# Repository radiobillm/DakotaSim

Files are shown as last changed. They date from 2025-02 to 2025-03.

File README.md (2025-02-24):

# DakotaSim – Piper Dakota Flight Simulator

DakotaSim is a PA-28-235 flight simulator to match our real plane's G3X-based panel. 

[Project Wiki](docs/home.md) is extensive and includes:

- A hardware build with custom-fabricated hardware
- SketchUp models
- Arduino-based HID throttle, switch, and trim controls
- Custom Air Manager instruments
- Parts and prices detail

## Downloads
- [DakotaSim SketchUp](https://github.com/radiobillm/DakotaSim/releases/download/v2.0-sketchup/dakota-sim.skp)
- [Arduino Sketches and boards.txt](https://github.com/radiobillm/DakotaSim/releases/download/v1.0-arduino/DakotaSim-Arduino.zip)
- [AirManager for Dakota](https://github.com/radiobillm/DakotaSim/archive/refs/tags/v1.0-airmanager-garmin.zip)
- [AirManager for Garmin 255/345](https://github.com/radiobillm/DakotaSim/archive/refs/tags/v1.0-airmanager-garmin.zip)

## Resources
- [Parts and Pricing](https://github.com/radiobillm/DakotaSim/blob/main/parts.md)
- [Community Discussions](https://github.com/radiobillm/DakotaSim/discussions)
- [Submit an Issue](https://github.com/radiobillm/DakotaSim/issues)

## Older Versions

### Dakota Sim for Honeycomb 
- [Description](Dakota-Honeycomb.md)
- [Sketchup](https://github.com/radiobillm/DakotaSim/releases/download/v1.0-dakota-honeycomb/dakota-honeycomb.skp)
  
### Desktop Sim
- [Desktop Sim](Desktop-sim.md)

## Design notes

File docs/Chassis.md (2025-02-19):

# Volair Chassis 

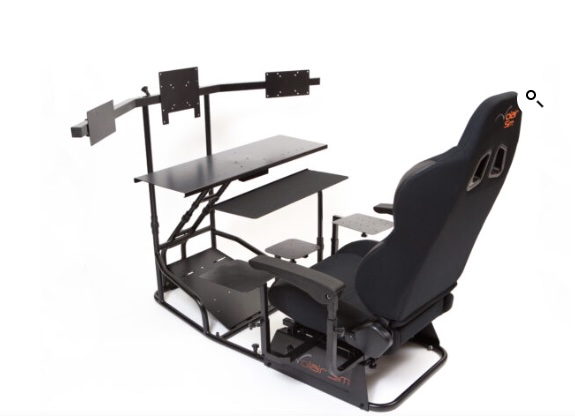
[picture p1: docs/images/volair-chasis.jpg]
Chasis


Volair’s Sim Chassis is sturdy and adjustable, the seat is comfortable.   The optional keyboard tray and armrests are nice.  I’ve not used any of the multiple plate mount attachments included.  

Their monitor support would be good for even a heavy single center monitor, but not for three.  I’ve replaced the monitor poles with rear table supports and built a floating shelf for the iTX computer case.

## Computer Shelf
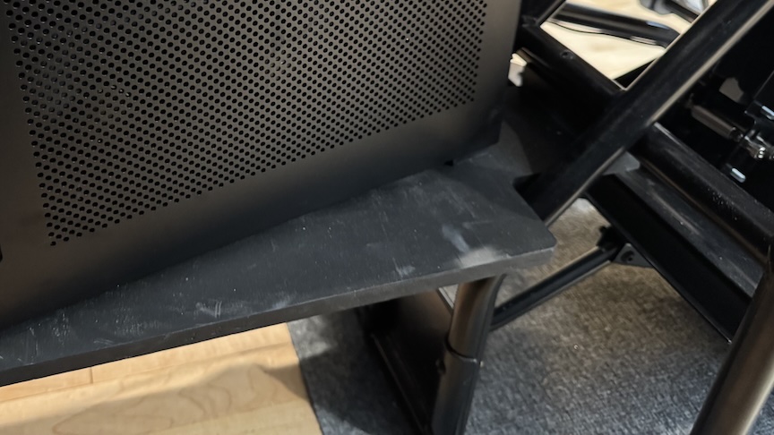
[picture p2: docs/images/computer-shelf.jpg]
Computer Self


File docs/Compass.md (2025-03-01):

# Compass

The whiskey-style Compass was purchased from SimWales (via caspajack on eBay), and it looks fantastic.

Mobiflight controls the compass, I had to adjust the suggested settings to use a Display Scale of 9000 and Transform $ * (-12.5).  The compass is powered with a USB 5V USB cable.

The compass stepper controller and ardunio are contained within a printed box that also holds the dimmer module.

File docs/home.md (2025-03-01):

# Dakota Flight Simulator

February 2025

Welcome to the documentation for my flight simulator project. This Wiki contains details about the construction, components, and software used in the simulator.

The sim was built to practice IFR flying using new avionics that match our real plane. It has also been a great opportunity to learn Arduino and explore my Onefinity CNC/Laser.

ChatGPT tells me that Piper has sold about 30,000 PA-28 series aircraft, compared to 45,000 Cessna 172/182 models. It’s surprising—and somewhat frustrating—for Piper pilots that most commercial flight sim products are Cessna-based. This project was built to create a sim that closely matches our plane.

The sim community is a gem.  After learning from so many projects and discussions, I felt guilty for never sharing my work.  This document includes the key components, build details, and lessons learned that I believe will be most helpful to others.

The current build would cost about $10,000. The project includes a breakdown of parts and prices.

## Front
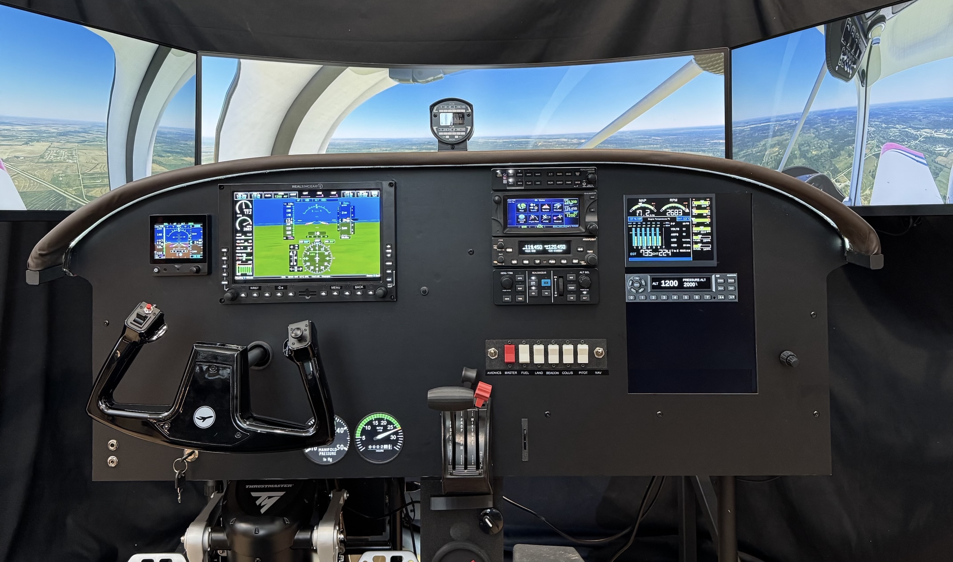
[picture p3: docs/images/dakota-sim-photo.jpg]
Dakota Sim


## Back
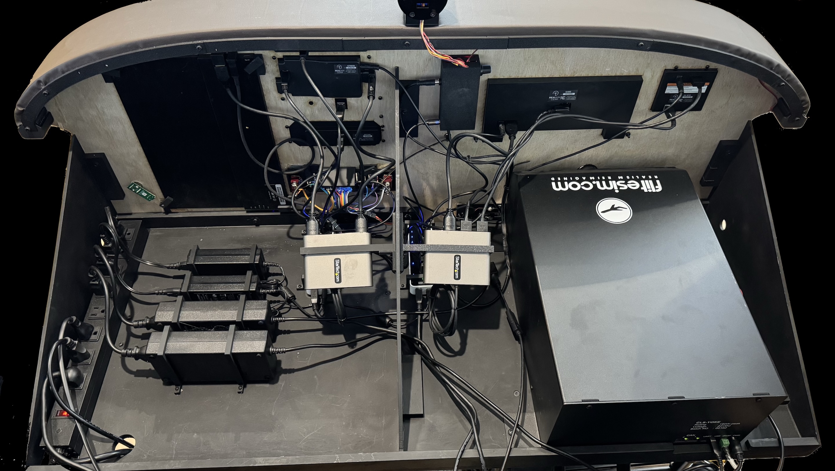
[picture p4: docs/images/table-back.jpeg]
Back of Panel


## Cockpit Structure
- [Avionics Panel](Panel.md) with laser cutting, auto wrap
- [Avionics Table](Table.md) with support, power, dimmer, hubs
- [Volair Chassis](Chassis.md) has a computer shelf
  
## Fabricated Controls
- [Throttle, Switch, & Panel Controls](Panel-Controls.md)
- [Center Stack , Brake, & Fuel](Center-Controls.md)
- [Trim & Flaps](Trim-flaps.md)
- [Compass](Compass.md)

## Arduinio
- [Arduino Hardware](Arduino.md)
- [Ardunio Software / FS2020](Arduino-sw.md)
  
## Other Purchased Hardware
- [RSG & Tigerfly Instruments](Instruments.md)
- [Flitesim Yoke & Thrustmaster Pedals](Yoke-pedals.md)
- [Monitors & Sound](Monitors-Sound.md)
- [Computer](Computer.md)

## Software
- [Software & Config Notes](Software.md)
- [Air Manger Instruments](AirManager.md)
- [SketchUp & Fabrication Files](SketchUp-Fabrication-Files)

## Parts List
- [Parts List & Pricing](Parts-Price.md)

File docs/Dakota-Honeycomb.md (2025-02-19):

# Dakota Sim with Honeycomb

In late summer of 2023 we bought a share of a PA-28-235 so I had a specific plane to target.  This second generation sim was a big upgrade to build a dedicated sim and recover my office desk.  It includes avionics to match our glass upgrade in the real-life plane. 

The heart of our new panel is a Garmin G3X and no X-Plane version is available so I moved to Microsoft and Windows. 

Details that are distinct from this older version may help those using standard Honeycomb throttle/yoke panels.

Dakota Sim with Honeycomb
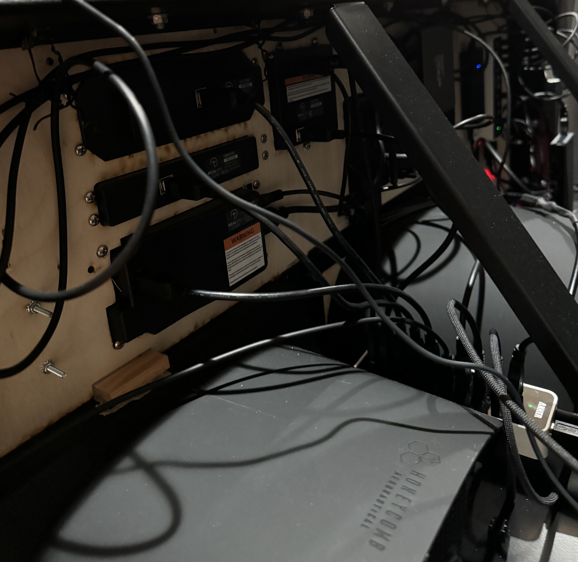
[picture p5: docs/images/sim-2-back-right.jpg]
Dakota Honeycomb Back

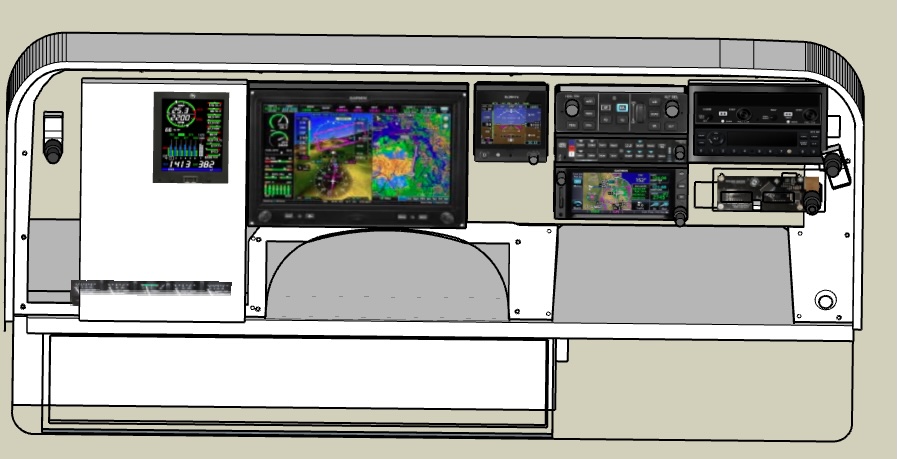
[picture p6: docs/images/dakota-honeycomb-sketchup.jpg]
Sketchup


## Panel
$500 [Volair panel](https://volairsim.com/product/volair-sim-avionics-panel-g1000/)

The Volair G1000 panel has a heavy-duty metal structure, back and table.  To fit my instruments I cut away most of the panel.  Into the frame I added a plywood back, cardboard center, and ACM front panel layers.

The -Honecomb Sketchup model has measurements from their panel made from test fitting cardboard itterations.

## Fabrication
$200 for [MakeATX](https://www.makeatx.com/custom-cutting) local laser cutting, 3 cardboard test iterations, final ¼” plywood back

$150 ACM front panel from [SendCutSend](https://sendcutsend.com/materials/acm/), great service 

## Panel and chassis
$600 Triple monitor stand from [Simfab](https://simfab.com/product/triple-monitor-mount-stand/), excellent quality

$1000 [Volair chassis](https://volairsim.com/product/volair-sim-flight-racing-sim-cockpit/) with arm rests and keyboard mount, excellent build

## Instruments
$1200 [G500](https://realsimgear.com/products/realsimgear-g500-avionics-panel	) from RealSimGear (originally for X-Plane with no G3X)

$550 [GTN650](https://realsimgear.com/products/realsimgear-gtn650-bezel-for-x-plane-p3d-and-fsx-steam) from RealSimGear

$350 [GFC500](https://realsimgear.com/products/realsimgear-gfc500-autopilot-for-x-plane-p3d-fsx) from RealSimGear

$350 [G5](https://realsimgear.com/products/realsimgear-g5-pfd-hsi-for-x-plane) from RealSimGear

$300 [GMA350](https://realsimgear.com/products/realsimgear-gma350-audio-panel-for-x-plane-p3d-fsx) from RealSimGear

$80 [Propwash Radio](https://www.propwashsim.com/)

## Panel LCD Displays
$70 [1920x1200](https://www.amazon.com/gp/product/B0DKFHZ8C8/) 14” left-side display for Air Manager compass, JPI engine, oil

$70 [1024x600](https://www.amazon.com/gp/product/B07VNX4ZWY/?th=1) 7” right-side touch display for Air Manager radio and transponder

$300 [1920x360](https://www.amazon.com/gp/product/B0CFY564ZQ) 24” low display for Air Manager fuel, manifold and tach

## Monitors and sound
$700 [Samsung Odyssey G9](https://www.amazon.com/gp/product/B0CP6HW894/) 49” Ultrawide monitor

$250 Two [Samsung 27” T35F](https://www.amazon.com/gp/product/B08FF3JQ28/) side monitors

$300 [Sonos Beam](https://www.sonos.com/en-us/shop/beam-b-stock-shadow), used Gen 1 (for an all Sonos-dude)

$85 [USB2GA Aviation Headset to USB Adapter](https://www.amazon.com/gp/product/B0CW3GLDM1/)

## Computer
In addition to the i9 running MSFS, I added this machine to Air Manager monitors

$230 MeLE [Mini PC](https://www.amazon.com/gp/product/B0CP3YL6J7/) for dedicated Air Manager

## Hubs, Power and Cables
$180 for two [StarTech USB to 4x HDMI](https://www.amazon.com/gp/product/B09BJWGPXR/)

$80 for two [Anker 10 Port 60W USB Hubs](https://www.amazon.com/gp/product/B00VDVCQ84/)

$21 [USB A to TOSLINK](https://www.amazon.com/gp/product/B0B2DBGKL3/r) for Sonos Beam audio

$20 [10A 12V Power supply](https://www.amazon.com/gp/product/B07MXXXBV8/) with custom hydra for RSG panel monitors

$57 [8 Outlet Metal Power Strip](https://www.amazon.com/gp/product/B0CJ55M1TH/)

$8 [12” USB-A Micro cable](https://www.amazon.com/gp/product/B095JZSHXQ/r)

$8 [12” USB-A to C cables](https://www.amazon.com/gp/product/B0BDFHBXQC/r)

$7 [18” HDMI cable](https://www.amazon.com/gp/product/B07ZC5Y3K2/r)

$9 [12” HDMI cables](https://www.amazon.com/gp/product/B0B5KN6853/)

$14 [6’ HDMI thin cables](https://www.amazon.com/gp/product/B00T58JLPI/r)
$10 [Displayport to HDMI adapters](https://www.amazon.com/gp/product/B09MTKHFKR/)

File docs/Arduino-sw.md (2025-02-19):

# Ardunio Software

One goal was to reduce software stacks which is why the input-only controls are HID and configured in MSFS.  ChatGPT wrote those the software software, it’s a marvelous tool for handling details and learning.

With FS2024 I may use MobiFlight or spad.next to better map and maintain.

Three Arduinos cover all input-only controls using the Joystick library.  The project includes code for each:
* Arduino Pro Throttle, Switch, TOGA, Carb Heat
* Arduino Micro Pro Trim and Flaps
* Arduino Micro Pro Parking Brake, Key/Start, Fuel Selector, and Rudder Trim

[Arduino Sketches and boards.txt](https://github.com/radiobillm/DakotaSim/releases/download/v1.0-arduino/DakotaSim-Arduino.zip)

## HID to Microsoft FS Controls

### Switch-Throttle
| Control | Button | FS-Control |
|---|---|---|
| Throttle | x | Throttle Axis |
| Mixture | y | Mixture Axis |
| Propeller Axis | z | Propeller Axis |
| Avionics Master 1 On | 2 | Avionics Master 1 On |
| Avionics Master 1 Off| 1 | Avionics Master 1 Off  |
| Master Battery On | 4 | Master Battery On |
| Master Battery Off | 3 | Master Battery Off |
| Set Electric Fuel Pump| 6 | Set Electric Fuel Pump |
| Set Electric Fuel Pump Off | 5 | Set Electric Fuel Pump Off |
| Landing Lights On | 8 | Landing Lights On |
| Landing Lights Off | 7 | Landing Lights Off |
| Beacon Lights On | 10 | Beacon Lights On |
| Beacon Lights Off | 9 | Beacon Lights Off |
| Strobes On | 12 | Strobes On |
| Strobes Off | 11 | Strobes Off |
| Pitot Heat On | 14 | Pitot Heat On |
| Pitot Heat Off | 13 | Pitot Heat Off |
| Nav Lights On | 16 | Nav Lights On |
| Nav Lights Off | 15 | Nav Lights Off |
| Set Anti Ice On | 18 | Set Anti Ice On |
| Set Anti Ice Off | 17 | Set Anti Ice Off |
| Auto Throttle to GA  | 19 | Auto Throttle to GA |

### Brake-Fuel
| Control | Key | FS-Control |
|---|-----|---|
| Magnetos Off | 1 | Magnetos Off |
| Magnetos Left | 2 | Magnetos Left |
| Magnetos Right | 3 | Magnetos Right |
| Magnetos Both | 4 | Magnetos Both |
| Magnetos Start | 5 | Magnetos Start |
| Parking Brakes On | 6 | Parking Brakes On |
| Parking Brakes Off | 7 | Parking Brakes Off |
| Fuel Selector 1 Off | 8 | Fuel Selector 1 Off |
| Fuel Selector 1 Left Aux | 9 | Fuel Selector 1 Left Aux  |
| Fuel Selector 1 Left  | 10  | Fuel Selector 1 Left |
| Fuel Selector 1 Right | 11  | Fuel Selector 1 Right |
| Fuel Selector 1 Right Aux| 12  | Fuel Selector 1 Right Aux |
| Rudder Axis | z | Rudder Axis |

### Trim-Flaps
| Control | Trim/Flaps | FS-Control |
|---|---|---|
| Set Elevator Trim Axis | x | Set Elevator Trim Axis |
| Retract Flaps | 04 | Retract Flaps |
| Flaps 1 | 103 | Flaps 1 |
| Flaps 2 | 302 | Flaps 2 |
| Flaps 3 | 451 | Flaps 3 |

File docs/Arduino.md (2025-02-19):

# Ardunio Hardware

Before this project, I had no prior experience with Arduino or circuit board assembly.  

Initially, I soldered IDC ribbon cables directly to the Arduino pins, using a separate connector for each control. Later, for the two additional Arduino Pros, I switched to using connectors soldered on the Arduino.

Renaming the USB HID device requires updating the boards.txt file, one is included.

See the software info

## Pin Mapping and Wire Bundles

This table documents the pin assignments and controls for the switch-throttle micro setup.

### Switch-Throttle - Micro

| PIN | USB | WIRE-COLOR | Cable |
|-----|-----|---|---|
| D13  | | Pitot Off | green |
| 3V | AREF| | |
| A0 | | Throttle | green |
| A1 | | Mixture | yellow |
| A2 | | Prop | orange |
| A3 | | Carb Heat On | blue |
| A4 | | Carb Heat Off  | purple |
| A5 | NC  | | |
| 5V | | 5V | red |
| GND  | | GND | brown |
| VIN  | | | |
| D14  | | GA | brown |
| D15  | | Nav Off | orange |
| D12  | | Avionics On | white |
| D11  | | Avionics Off | grey |
| D10  | | Master On | purple |
| D9 | | Master Off | blue |
| D8 | | Fuel On | green |
| D7 | | Fuel Off | yellow |
| D6 | | Landing On | orange |
| D5 | | Beacon On | brown |
| D4 | | Beacon Off | white |
| D3 | | Collision On | grey |
| D2 | | Landing On | red |
| GND  | | GND | black |
| RESET| | | |
| D0 | | Collision Off  | purple |
| D1 | | Pitot On | blue |
| D17  | | | |
| D16  | | Nav On | yellow |

### Brake-Fuel Pro Micro

| PIN | USB | WIRE-COLOR | Cable |
|---|-----|---|---|
| TX/RX/GND| | black | Key+Brake|
| GND | | grey | Key |
| D2 | | purple | Key |
| D3 | | blue | Key |
| A6/D4 | | green | Key |
| D5 | | yellow | Key |
| A7/D6 | | orange | Key |
| D7 | | | |
| A8/D8 | | orange | Rudder |
| A9/D9 | | | 7-12V |
| GND | | black | Rudder |
| RST | 5V  | orange | Rudder |
| A3/D21  | | brown | Fuel |
| A2/D20  | | red | Fuel |
| A1/D19  | | orange | Fuel |
| A0/D18  | | yellow | Fuel |
| D15 | | green | Fuel |
| D14 | | yellow | Park |
| D16 | | red | Park |
| A10/D10 | | | |

### Trim-Flaps Pro Micro

| PIN | USB | WIRE-COLOR | Cable |
|---|-----|---|---|
| TX/RX/GND| GND | black | Flaps | 
| D2 | | white | Flaps |
| D3 | | grey | Flaps |
| A6/D4 | | purple | Flaps |
| D5 | | blue | |
| A7/D6 | | | |
| D7 | | | |
| A8/D8 | | black | Trim |
| A9/D9 | | | 7-12V |
| GND | RST | | |
| 5V | | | |
| A3/D21  | | | |
| A2/D20  | | | |
| A1/D19  | | | |
| A0/D18  | | | |
| D15 | | | |
| D14 | | | |
| D16 | | | |
| A10/D10 | | | |

### Compass Pro Micro

| PIN | USB | WIRE-COLOR | Cable |
|---|-----|---|---|
| TX/RX/GND| | | |
| GND | | | Compass  |
| D2 | | | |
| D3 | | | |
| A6/D4 | | | |
| D5 | | | |
| A7/D6 | | | |
| D7 | | | |
| A8/D8 | | | |
| A9/D9 | | | 7-12V |
| GND | RST | 5V | |
| 5V | | | |
| A3/D21  | | | Compass  |
| A2/D20  | | | Compass  |
| A1/D19  | | | Compass  |
| A0/D18  | | | Compass  |
| D15 | | | |
| D14 | | | |
| D16 | | | |
| A10/D10 | | | |

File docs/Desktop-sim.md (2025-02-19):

# Desktop Sim

Desktop Sim

I retired in early 2023 and decided to resume flying after a 30 year break.  The first step was setting up a desktop sim. 

My first iteration was X-Plane based system on my office desk which had a Mac Studio and Samsung ultrawide monitor.  The only item still used from that version is my Air Manager license.

Below are the components:

$60 [X-Plane](https://www.x-plane.com/) 

$30 AeroSphere [PA-28-235](https://store.x-plane.org/Piper-PA-28-235-Charger-Cherokee-235_p_1605.html) to match my real life plane

$750 Honeycomb [yoke](https://flyhoneycomb.com/collections/bestseller/products/alpha-flight-controls) and [throttle](https://flyhoneycomb.com/collections/bestseller/products/bravo-throttle-quadrant) plus Logitech [rudder pedals](https://www.logitechg.com/en-us/products/flight/flight-simulator-rudder-pedals.945-000024.html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)

$30 Rudder pressure rolls back the Aeron chair, added [locking chair casters](https://www.amazon.com/gp/product/B0BKLSQVJ4/)

$300 [Air Manager](https://www.siminnovations.com/air-manager/) and [Knobsters](https://www.siminnovations.com/shop/knobster/) made realistic instrument use

$120 Moved instruments to a [14” portable touch display](https://www.amazon.com/gp/product/B0C4TCHK1S/r)

$100 More panel display from an old iPad and [Luna display dongle](https://shop.astropad.com/collections/luna-display-mac-and-pc?) 

$300 Added Mac-compatible [GNS530 from FlightSimBuilder](https://flightsimbuilder.com/products/gns-530-fs2020-campatabl) to learn buttonology

$70 Stay Level [touch bracket](https://staylevelavionix.com/shop/touch-bracket), soon replaced with…

$20 Fabricated [channel](https://www.dkhardware.com/satin-anodized-1-2-aluminum-u-channel-dv750a-ccp24-24-stock-length-product-3696857.html) for glass table to mount yoke and throttle under glass desk for space

$45 Added 3 [flexible phone mounts](https://www.amazon.com/gp/product/B07726TH68/) to hold displays and the 430, these worked well

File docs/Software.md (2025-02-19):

# Dakota Sim Software

## RV-10
The RV-10 was early with G3X and TDS GTN support.  Its power and handling are similar to the low-wing Piper Dakota we fly.

## TDS GTNxi Pro

The GTN650 was an essential piece in my setup. My move from X-Plane to MSFS was largely driven by the need for a Garmin G3X that integrated properly with the GTN.  The current G3X from Asobo is very good and I’m grateful to TDS for integrating with it.

TDS builds a high quality instrument and their support has been superb, both for me and others on Discord.  They don’t over-promise and they take actual bugs seriously.

One downside is that each time you load MSFS you need to use TDS admin to set the nav source from the 750 to 650.  Another downside is that I’m still not able to maximize the window in the RSG screen without a title bar.  Either the bar shows and the window can be sized, or the bar is hidden and the app window is about 30% of the size needed. I simply pull the title bar outside the instrument.

I’ve used the PMS version which works not as well but mostly was not integrated with the G3X.  My first GTN was for X-Plane from RealityXP, it worked OK but their constant license renewal was annoying.

## MSFS Popup Panel Manager

Thanks to Stanley Kwok for creating and sharing his popout manager. This free tool makes it possible to use a touch display and also automates popout and placement when flying.  

It’s hard to understand how Microsoft continues to ignore touch instruments.

Unfortunately, I still need a mouse on standby because my G500 panel frequently ignores touch input on the left side of the display. This isn’t a hardware issue—other applications recognize touch input in the same area. Since the G3X is my primary instrument, this matters quite a bit and is one of the main reasons I moved from X-Plane to MSFS.

## MobiFlight

MobiFlight is an open source bridge between hardware and sims.  It’s essential for my GNC255 radio built by a MobiFlight expert. MobiFlight also controls the compass.  I don’t know the software yet but for better control options I am considering moving my own arduino instruments to it.

## RealSimGear MSFS Device Interface

Since my setup includes five RealSimGear instruments, I rely heavily on their MSFS device interface. I’m glad to see they’ve become more active on Discord and in support channels again, though their primary focus now appears to be commercial SR22 simulators.

My setup still includes a G500 panel that I originally purchased during my X-Plane era.

Through experimentation, I’ve remapped this hardware to function with G3X commands, using the command.ini file. To improve usability, I’ve labeled certain G500 buttons for G3X functions.

While this setup is a little janky, it works well enough that I don’t need to buy another $1,200 RealSimGear instrument or build a custom one from scratch.

The command.ini in the project also has GMA350 audio panel knobs, the default only maps critical buttons.

I suspect the RealSimGear device interface is responsible for the total loss of controls that occurs about 30 minutes into a flight session in MSFS.

Controls only return if I open the Controls menu and then exit back into the flight, which suggests an interface-related issue. Since this only happens when RSG is loaded, I’m considering switching to spad.next as an alternative.

## LittleNavMap

LittleNavMap is excellent for quickly creating flight plans, which I sometimes export to the GTN.

I also use it to monitor my flight progress and manage descent slopes efficiently.

## RealVNC

Spending hours in the cockpit chair with a keyboard tray and a sea of monitors can be tiring.  RealVNC has been great for some projects working upstairs in an office setting.  Real VNC also lets me find lost monitors and work when the screen is covered by panel.

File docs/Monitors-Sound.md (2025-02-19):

#Monitors and Sound

## Main Monitors

name

Since I was already happy with a previous model, I upgraded to Samsung’s 49” Ultrawide Odyssey G9 as my center monitor, paired with two Samsung 27” side monitors.  

## Monitor Stand
name

The SimFab Triple Mount monitor stand is beefy and good without angled front but without side stands. Vertically aligning side monitors took all the adjustment available and then some to match the ultrawide center screen.

All three monitors use HDMI on the monitor connected to one HDMI and two DP ports with adapters on the 4080 card.  For some reason, the ultrawide monitor’s DisplayPort connection was not recognized, and after spending too much time troubleshooting, I gave up and used HDMI instead.  Also, I goofed by buying an Intel i9 processor without graphics.  

## Panel Monitors

The panel includes six monitors, all powered through a USB-to-HDMI adapter:

* RealSimGear G500, GTN, and G5
* A low-mounted display for Manifold and Tach gauges powered by USB-C
* A right-side monitor for the JPI Engine Monitor and Transponder

This setup mostly works well, but occasionally Windows 10 forgets the display arrangement or loses touchscreen functionality.  

In an earlier setup, I had nine total displays, but Windows 10 frequently dropped them from the configuration. To fix this, I added a dedicated mini PC to handle Air Manager instruments. Now that I’ve reduced the number of displays, the mini PC is no longer necessary.

## Sound

A Sonos Beam works well using a USB-TOSLink-HDMI connection.  The beam rest on L brackets fabricated to hang from the monitor stand.

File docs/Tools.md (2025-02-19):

This major upgrade was the excuse needed to upgrade my shop with these tools:

$6800 [Onefinity Foreman](https://www.onefinitycnc.com/product-page/elite-series-foreman-48-x48-cut-area) 4’x4’ CNC, [PwCNC spindle](https://pwncnc.com/products/spindle), [44W laser](https://www.onefinitycnc.com/product-page/onefinity-j-tech-44w-octo-pro-laser-worlds-most-powerful-diode-laser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), and dust boot

$950 [FlexiSpot E7Q](https://www.flexispot.com/flexispot-odin-4-leg-standing-desk) 4-leg standing to park my CNC above my planner and joiner

$840 [Bambu P1P](https://us.store.bambulab.com/products/p1p) 3D printer, enclosure upgrade (order mistake, they would not exchange)

I replaced the panel, table, yoke, throttle, rudder pedals and radio.  I don’t need all the Air Manager monitors nor the Air Manager computer.  I’m using all the instruments and especially design and layout lessons from the prior panel.

You can see the total products and prices used and build details in the main section above.

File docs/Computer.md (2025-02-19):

# Computer

Built from the parts list below including an i9 and 4080, performance is good enough to use mostly max settings with three monitors plus five in the panel.  The system was originally purchased for under my office desk, otherwise the small case is not worth the careful work squeezing components together.

I mistakenly ordered an i9 without graphics.

## PC Components

| Component | Product | Price | Where |
|---|---|---|---|
| **CPU** | [Intel Core i9-14900KF 3.2 GHz 24-Core Processor](https://pcpartpicker.com/product/MJRFf7/intel-core-i9-14900kf-32-ghz-24-core-processor) | $416.94 | [Amazon](https://www.amazon.com) |
| **CPU Cooler** | [Deepcool LT520 85.85 CFM Liquid CPU Cooler](https://pcpartpicker.com/product/dqXJ7P/deepcool-lt520-8585-cfm-liquid-cpu-cooler) | No Prices Available | |
| **Thermal Compound** | [Arctic Silver 5 High-Density Polysynthetic Silver 3.5 g Thermal Paste](https://pcpartpicker.com/product/gJmFf7/arctic-silver-5-high-density-polysynthetic-silver-35-g-thermal-paste) | $7.95 | [Amazon](https://www.amazon.com) |
| **Motherboard** | [Asus ROG STRIX B760-I GAMING WIFI Mini ITX LGA1700 Motherboard](https://pcpartpicker.com/product/vVy2FT/asus-rog-strix-b760-i-gaming-wifi-mini-itx-lga1700-motherboard) | $189.99 | [Newegg](https://www.newegg.com) |
| **Memory** | [Corsair Vengeance 32 GB (2 x 16 GB) DDR5-6400 CL32 Memory](https://pcpartpicker.com/product/XqgFf7/corsair-vengeance-32-gb-2-x-16-gb-ddr5-6400-cl32-memory) | $102.99 | [Newegg](https://www.newegg.com) |
| **Storage** | [Crucial P5 Plus W/Heatsink 2 TB M.2-2280 PCIe 4.0 X4 NVME Solid State Drive](https://pcpartpicker.com/product/xFmmP6/crucial-p5-plus-wheatsink-2-tb-m2-2280-pcie-40-x4-nvme-solid-state-drive) | $169.00 | [Amazon](https://www.amazon.com) |
| **GPU** | [Asus ProArt GeForce RTX 4080 16 GB Video Card](https://pcpartpicker.com/product/ff66Mp/asus-proart-geforce-rtx-4080-16-gb-video-card) | No Prices Available | |
| **Case** | [Lian Li A4-H20 X4 Mini ITX Desktop Case](https://pcpartpicker.com/product/ff66Mp/lian-li-a4-h20-x4-mini-itx-desktop-case) | $154.99 | [Amazon](https://www.amazon.com) |
| **Power Supply** | [Corsair SF750 (2018) 750 W 80+ Platinum Certified Fully Modular SFX Power Supply](https://pcpartpicker.com/product/ff66Mp/corsair-sf750-2018-750-w-80-platinum-certified-fully-modular-sfx-power-supply) | No Prices Available | |

### Base Total: **$1044.86**

[Full PCPartPicker List](https://pcpartpicker.com/list/qsLdJy)

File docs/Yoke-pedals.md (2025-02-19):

# Flitesim Force Yoke

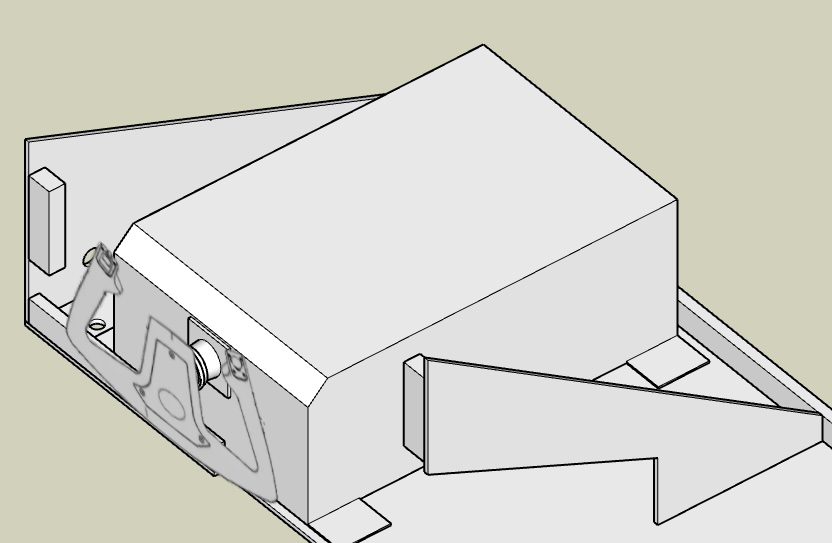
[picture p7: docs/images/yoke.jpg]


The Flightsim Force Yoke works well and brings a fun realistic dimension flying the sim.  The yoke box is much bigger than a Honeycomb which became the final straw forcing me to build a fully custom table, panel, and glare shield.

# Thrustmaster TPR Pedals

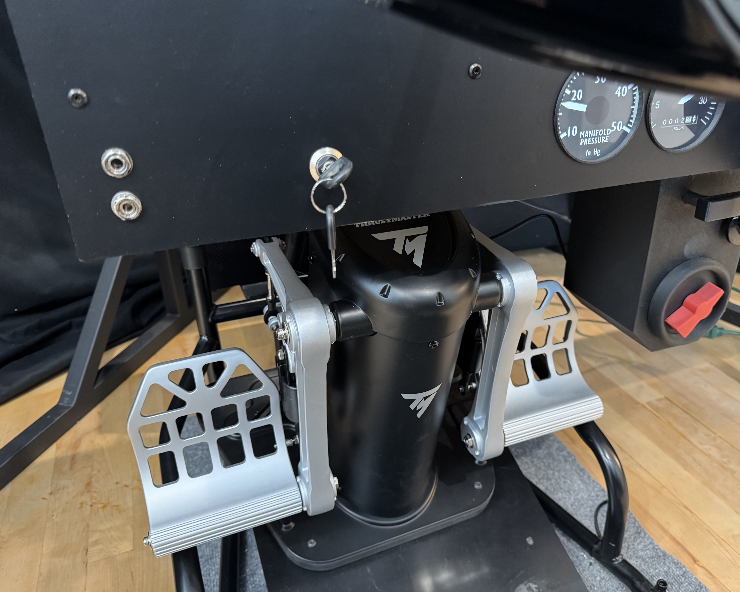
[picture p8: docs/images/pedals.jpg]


Thrustmaster TPR pedals have worked well so far as a nice upgrade from the Logitech set.  The Volair chassis has a framed well area and the pedals are designed for a flat floor.  I solved it by cutting a ¾” spacer that matched the Thrustmaster base.  The spacer has threaded inserts that align with the top Volair slots and an extra hole drilled below, then inserts for the four Thrusmaster base bolts.  This approach has worked well so far even while the right pedal almost hits my center box.

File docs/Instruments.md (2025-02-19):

# Insrtruments

## GNC255 Radio

One of my favorite devices in this build is the GNC255 radio, designed and built by Tigerfly.. I have an early build and don’t know if it will be a product.  You can usually find Tigerfly helping others on the MobiFlight Discord.

The radio has realistic knobs and buttons, a bright white OLED display and photo sensor for dimming.  Like the real Garmin, Tigerfly’s software includes frequency database lookup.  

Tigerfly was especially helpful getting me started with MobiFlight and I hope he’ll extend the line with a matching transponder and/or share the design.

## RealSimGear

The setup includes these instruments

* G5 works well with the air manager instrument with buttons mapped
* G500 is from an earlier sim and for my G3X, I don’t love it
* GTN650 works well except the home button is fake
* GFC500 AutoPilot is very good, except their vertical trim knob is flimsy
* GMA350 Audio works, I don’t see on their website anymore 

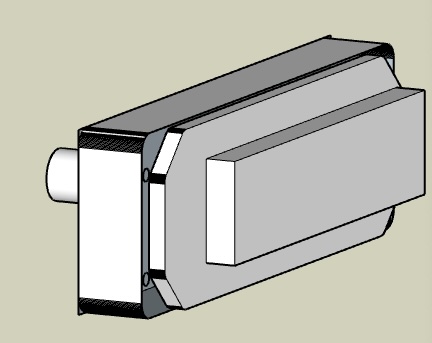
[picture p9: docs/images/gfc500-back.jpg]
GFC500 Model


Sketchup models are organized to use for 3d planning or just keeping the faceplate-cut to export for laser or cnc.

## Compass

The whiskey-style Compass was purchased from SimWales (via caspajack on eBay), and it looks fantastic.

Mobiflight controls the compass, I had to adjust the suggested settings to use a Display Scale of 9000 and Transform $ * (-12.5).  The compass is powered with a USB 5V USB cable.

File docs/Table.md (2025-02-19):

# Avionics Table

## Support Table
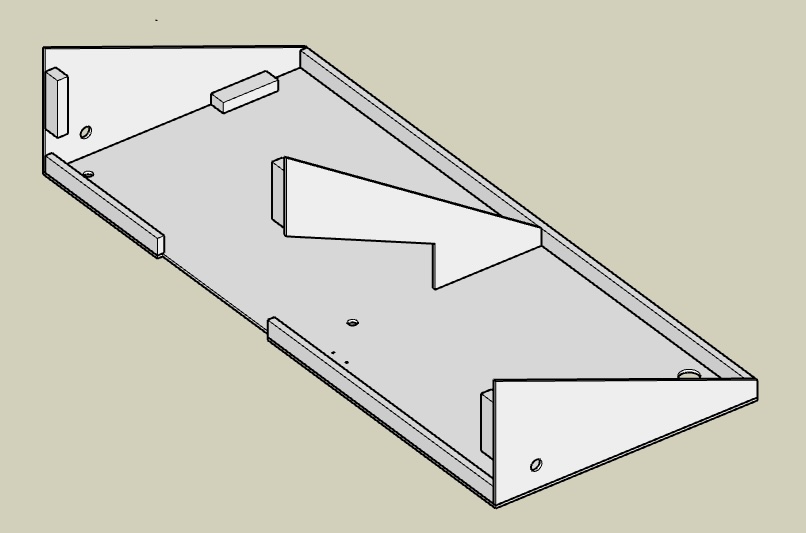
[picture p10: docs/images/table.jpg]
Avionics Table


The support Table is ½” plywood with edge and side pieces to replace the chassis metal. 

The side pieces are laser cut from 5.2mm plywood at 7mm/sec.  Laser lines etched into the table base made it clear where to cut and align the rail, sides and blocks.

The panel and table are setup for a left side yoke to be centered on the chair. The left side metal yoke box and the right side metal power strip help keep the assembly rigid. 

For support I replaced the original chassis monitor stand.  A 3/4”x24” threaded water pipe was cut in half and flanges attached to each end.  Those fit perfectly into the chassis to support the table.  The table and supports are painted flat black.  M6 bolts attach the table to the flange and front metal square tube, these holes are drilled after aligning and squaring the table but not in the.  A right-side leg supports the overhand and keeps the table stable.

## Power and Hubs

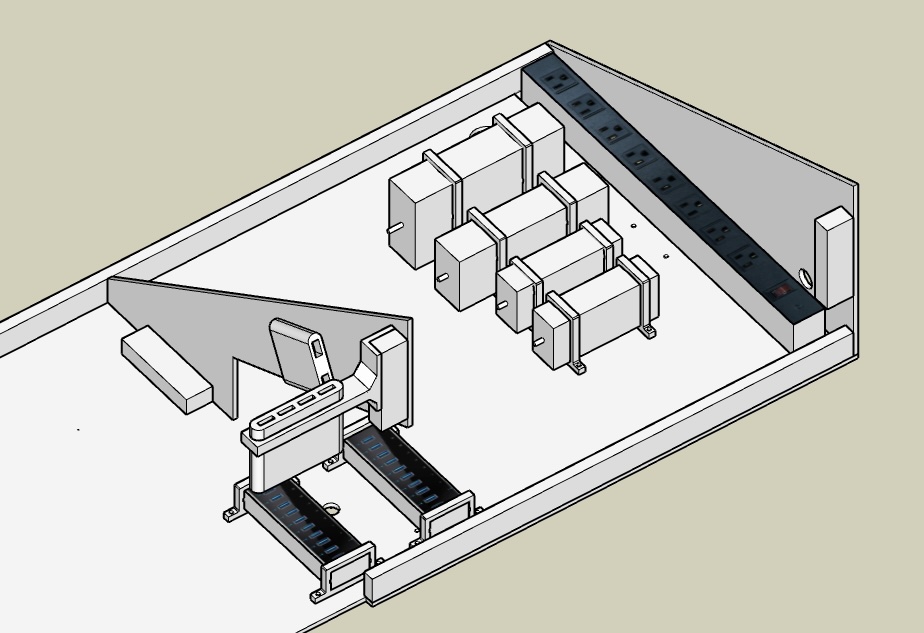
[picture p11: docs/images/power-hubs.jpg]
Power and Hubs


For aesthetics and easier troubleshooting I took time for the component layout above and under the table and designed and printed holders for power supplies, USB hubs, and HDMI adapters.

## LED Dimmer
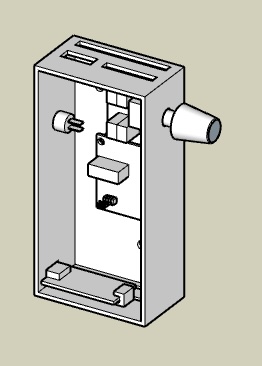
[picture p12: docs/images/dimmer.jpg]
LED Dimmer and Compass Arduino


A printed box with lid mounted on the back of the panel houses an Arduino Pro Micro and compass stepper motor driver plus a dimmer connected to the compass and under-glare shelf lighting.  A hydra end from the 12V power supply powers the dimmer.

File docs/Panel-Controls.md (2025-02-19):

# Fabricated Controls
## PA28 Throttle

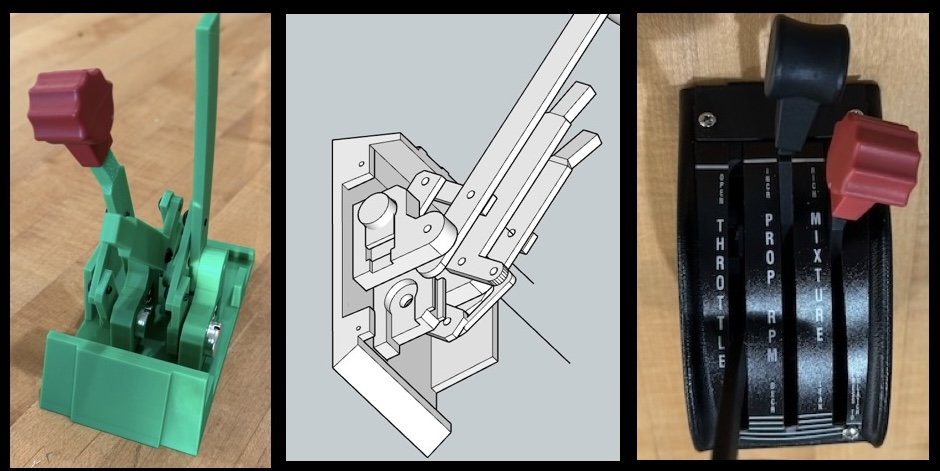
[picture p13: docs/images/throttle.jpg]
Custom PA-28 Throttle


I started by buying a real replacement throttle assembly trim and label, then designed and 3D printed the body.  

To fit the closely spaced throttle, prop, and mixture levers, I used bellcranks to offset the potentiometers.

The M4 screws into 3mm PLA holes were not strong enough on their own and required glue for reinforcement. Threaded inserts would be a better solution, as the tight space makes soldering and adjustments difficult.

Label strips are glued to the top of the trim cover under a printed trim plate.

## Switch Panel

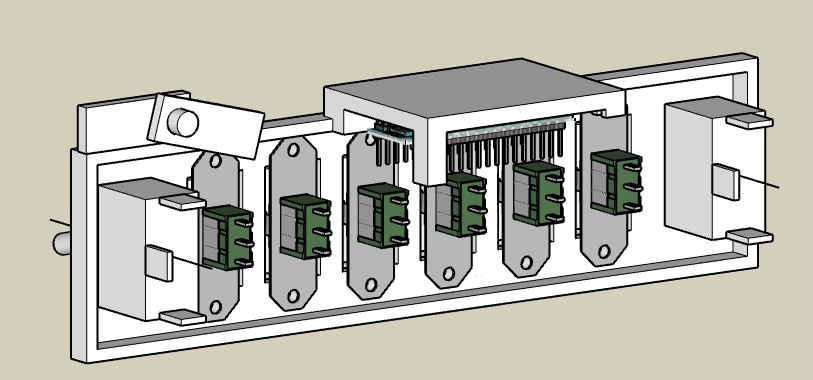
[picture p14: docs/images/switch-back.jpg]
Switch Panel Back


The hard part for the switch panel was sourcing rocker switches that match a real PA28.  I ordered a few alternatives but never found half-width rockers that could be ganged together to match the real set, nor found suitable grey covers.  

As a future improvement, I plan to laser engrave labels onto the switch covers for a more authentic look.

An Arduino Micro in the switch panel handles the switches, throttle, Carb Heat lever, and TOGO button. 

## Carb Heat

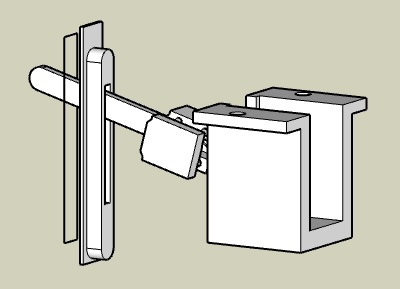
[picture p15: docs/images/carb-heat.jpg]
Carb Heat Lever


The Carb Heat lever is printed to sandwich the end of a metal toggle, the assembly also has a switch holder under the table.  A printed panel trim insert keeps the lever sliding vertically with a realistic feel.  MSFS offers Anti Ice On or Off, but no variable carb heat setting like a real PA28.

### Key Switch

I ordered the SimWales Key Switch from caspajack on eBay. The spring mechanism is well-designed, and the build quality is excellent.

One challenge was the table height meant moving the switch a little lower than in real life, even after cutting off the top of the assembly. The switch was disabled and the faceplate removed.  When reassembling I first aligned the key position and then the pin so it hits the spring on start. 

## Headset

The headset speaker and microphone jacks are connected via a USB Aviation adapter.

Installation Details:

* The adapter’s casing was removed, allowing me to use the jack nuts directly on the panel.
* Since the panel is ¼” thick, a relief pocket is needed on the backside (not currently included in the model).
* The USB board is glued to the back of the panel, as it lacks a dedicated case.

A prior ACM panel grounded the mic so it became unusable with PilotEdge, which was solved by printing bushings to insulate the jacks.  This bushing is unnecessary with plywood.

## Bezels

Simple bezels are printed for the yoke, manifold, and tach gauge, carb heat and togo switch openings.  I may build a bezel for the JPI Engine monitor.

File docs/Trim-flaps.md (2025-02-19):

# Trim and Flaps

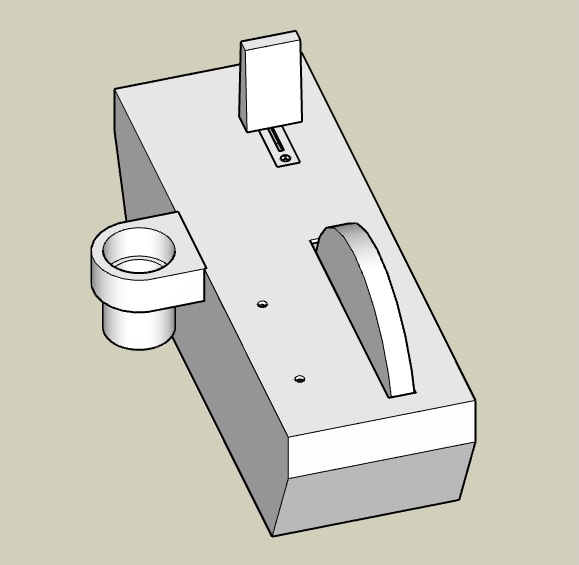
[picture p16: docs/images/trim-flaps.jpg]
Trim and Flaps


For a more realistic layout, I mounted an Elevator Trim box on the right side of the chair, where a pole mount normally holds the keyboard tray.  The box has a Trim Wheel, 4-position Flaps Paddle.  Inside the box an Arduino Micro is glued with the USB port facing down. 

The Trim Wheel, potentiometer, and switch were salvaged from a Desktop Aviator unit I purchased on eBay.

I may upgrade to a powered trim wheel with a geared position indicator in the future.  PA28 pilots will recognize that flaps are set with a long floor-mounted lever, the 172- flap lever is not realistic but at least it is centered near the floor.

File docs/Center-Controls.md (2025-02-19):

# Center Stack Controls

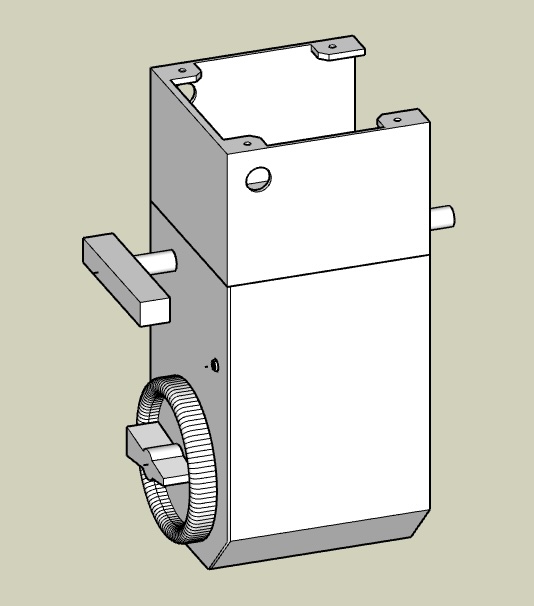
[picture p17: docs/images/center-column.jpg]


A bolted support box under the table houses:

✔ Parking Brake

✔ Fuel Selector Switch

✔ Rudder Trim

✔ Arduino Pro (which also controls the key switch)

Due to the limitations of my 255mm 3D printer bed, the column is built from two stacked boxes. The parking brake is mounted to the ceiling of the lower box.

However, the top box is too small to allow easy internal access. A better approach would be to side-mount the brake and leave an open column for easier maintenance.

The Arduino is floating with no mount, it also controls the key switch.

## Parking Brake 

I ordered the SimWales Parking Brake (designed for a Cessna 172) from caspajack on eBay, and it works well.

However, Parking Brake On and Off controls do not function correctly in either the Cessna 172 or RV-10. As a workaround, I mapped the Off control to Parking Brake Toggle for reliable operation.

The brake main rod stop was removed to remove the faceplate.  Be careful when rotating the brake assembly to preserve normally in and brake-off horizontal, vs pull and rotate brake-on vertical.  The switch pin can be flipped to an alternate hole.

## Fuel Selector 

The Fuel Selector switch is simply a trim piece over a 5-selector switch.  

On a real Piper PA-28-235, the fuel selector is located on the center firewall and has five fuel positions:

1. Off
2. Left Tip
3. Left Main
4. Right Main
5. Right Tip

I was unable to find any published designs for the plastic trim piece, nor could I find an MSFS Dakota or any PA-28 with a four-tank configuration.

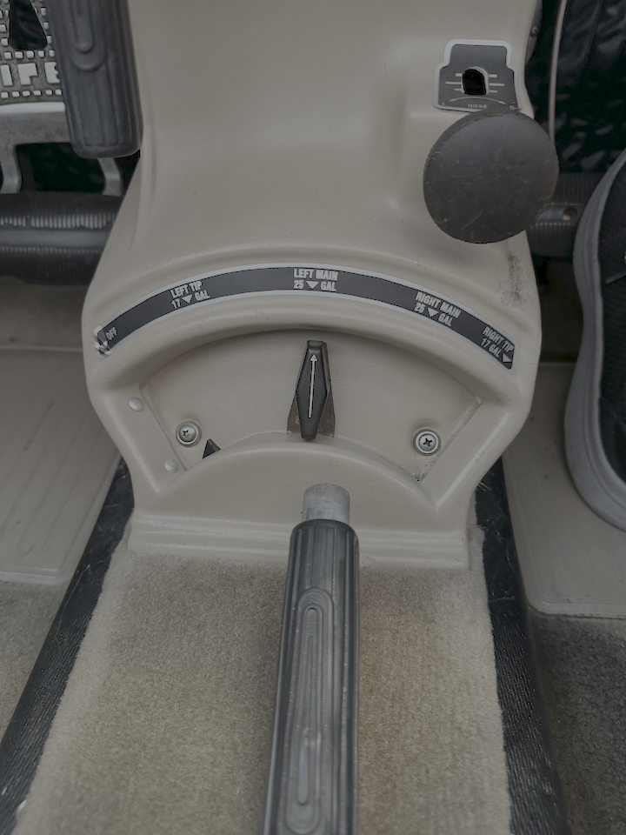
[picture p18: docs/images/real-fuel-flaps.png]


## Rudder Trim

The rudder trim uses a potentiometer identical to those used for the throttle levers. It is mounted with a custom-printed bracket for the center column.

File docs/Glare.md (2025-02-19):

# Glare Shield 

The glare shield has been the most time-consuming part of the build. My trepidation building one had me hacking the Volair panel for too long. But my first glare shield is only OK.

## Back Structure

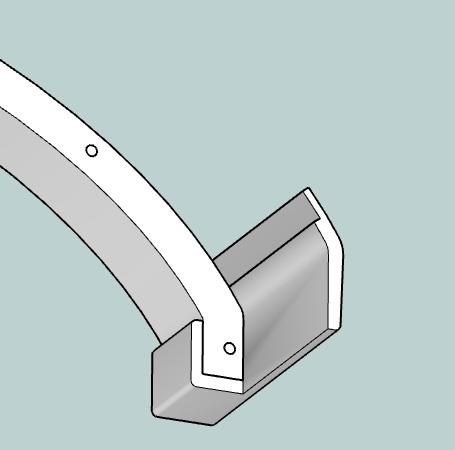
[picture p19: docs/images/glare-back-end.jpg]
Glare Sheld Back


The curved vertical back of the glare shield (glare-base layer) is built from two laminated ½” plywood pieces, cut on the CNC. 

## Horizontal Shelf

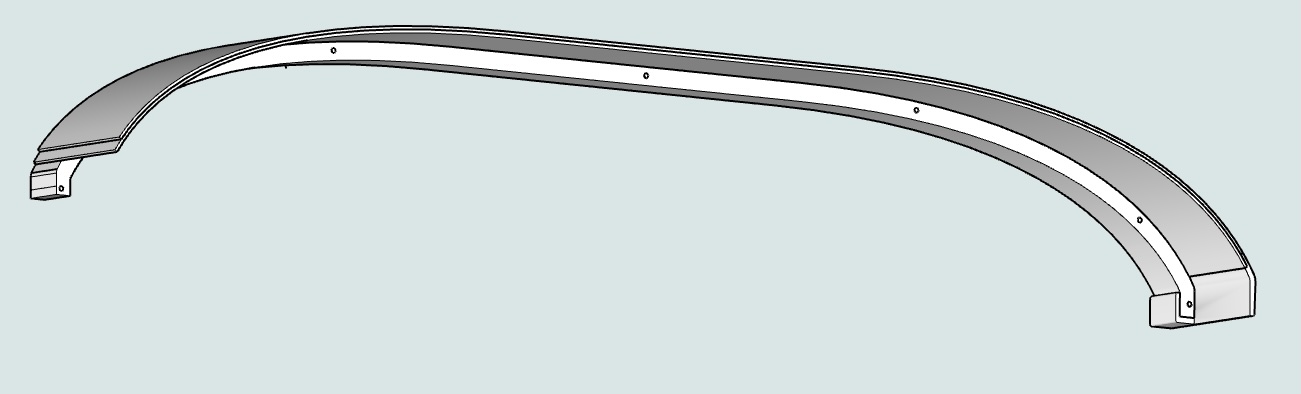
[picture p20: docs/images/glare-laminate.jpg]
Glare Laminated Shelf


For the horizontal face, I initially scored and steamed ⅛” plywood, attempting to bend it around the PA-28’s tight end curves.  This was slow and the material kept splitting. The process was slow, and the material kept splitting.  So I abandoned the approach instead printing end pieces for the steep curve (end-right/left). These are notched for the wood layers and glued with construction adhesive, it worked well.  

The plywood and 3D-printed end assembly created a strong base for laminating two layers of 2.6mm plywood, which I formed and clamped to the curved back and end sections.

A second ¼” plywood curve was added to reinforce the structure and create a pocket for the panel. A thin ¼” plywood trim was also added to house the LED rope and provide a termination point for the foam covering. The LED rope doubles as a piping cord, securing the vinyl cover material in place.

The entire assembly was painted flat black before applying the foam padding and vinyl cover.

Long M4 screws were installed through the back to secure the vinyl trim and attach the glare shelf to the panel. Although I forgot to include screw inserts, the friction fit is strong enough to hold it in place.

When wrapping the ¼” neoprene foam, I made the mistake of applying strong adhesive to the front edge first. I realized the foam wouldn't stretch or compress well around sharp curves. Attempting to soften it with a heat gun only caused it to break down. I had to cut V-gaps to fit the shape, but those gaps are still visible through the thin vinyl cover.

The assembly is then covered with a flexible leather-like adhesive-backed furniture patch material.  This also looks home-made because the curves and corners don’t tuck.  Next time I would either persuade my wife, learn or buy a sewn leather wrap formed for the surface.

## Printed Ends and Trim

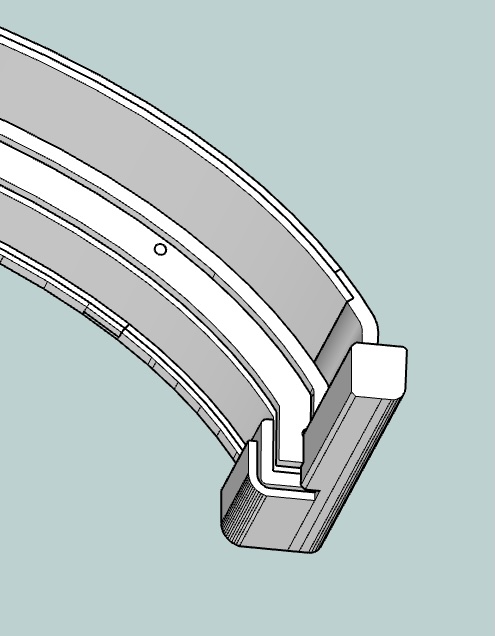
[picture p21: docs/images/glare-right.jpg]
Glare End


Because the vinyl ends peel off, I then designed and printed relatively complex end caps.  

The back vinyl is covered with a trim cap.  The trim cap is from about 6 pieces printed and glued.  Another material laser or CNC cut would be cleaner and faster.

Finally, the panel is lit with LED rope which does double duty by tucking in the vinyl.  The LED strip glows nicely and can be cut at about 2” intervals.  Leads are soldered and run behind the panel and are terminated with a 2-pin connector for the dimmer box.

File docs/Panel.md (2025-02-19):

# Avionics Panel

## Laser Cutting Plywood
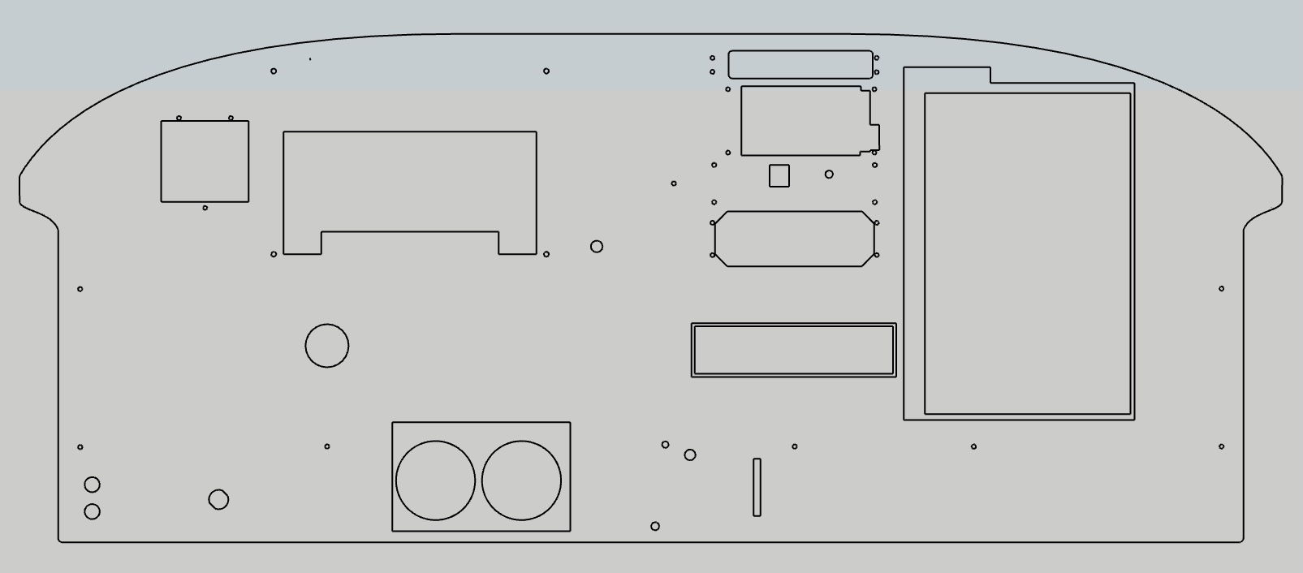
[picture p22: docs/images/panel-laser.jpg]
Panel


The firm upgrading our avionics supplied a pdf which became the scaled panel layout (\panel\01l-panel-pdf).  I made a few compromises because my panel rides on the front of a support table and for the 14” right side monitor.

The panel is from two 3.2mm Sandee layers laser cut and glued together.  The back layer has larger openings that outline the switch and monitors.  Front layer cutouts for the monitors and switch panel are smaller for a recessed mount.  Before this two-layer build I had used the CNC to cut and recess openings.  But after finding build conflicts I moved to two layers, because I had the material and could quickly cut with the laser.

Each item on the panel has a group and layers to model in 3D.  Templates from RealSimGear I found did not work well on earlier sims, mine are from trial and error with cardboard test pieces.

My 44W laser cuts the 2.6mm plywood at 15 mm/second and 100% power.

To produce an file for cutting the panel requires showing the *-cut layer within each group. These layers should be tagged as “-cut”.  The switch and monitors are recessed with cut lines for each layer.

## Embedded Displays
To fully embed LCD displays and have flush instruments my prior panel was from a ¼” plywood back, ½” thick cardboard center and ¼” ACM front.  It looked great, but was complicated and unrealistic because our real instruments are surface mounted.

Initially, I experimented with different mounting designs—including tabs—but found that toggle brackets provided the most secure fit. These same brackets were also used to mount the right-side monitor and switch assembly.

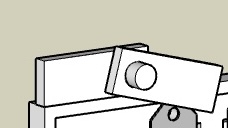
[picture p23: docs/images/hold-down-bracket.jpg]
Hold Down Brackets


## Auto Wrap
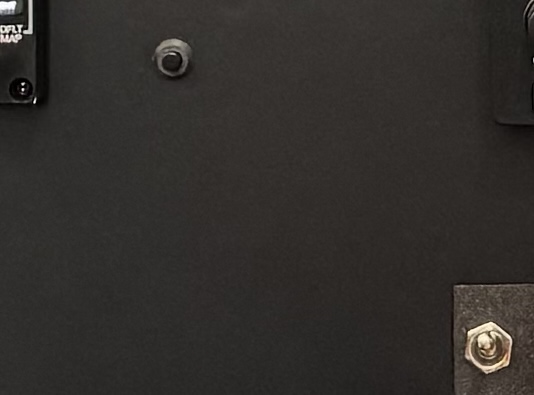
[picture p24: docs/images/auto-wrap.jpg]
Auto Wrap Finish


The panel front is covered with **black matt auto wrap** which worked surprisingly well. My main lesson was to apply over a sanded clear poly.  Even after wiping twice, bare plywood held small flakes and every spec showed through the wrap. I used a heat gun to stretch slightly and cut openings after applying.  If building a second model I’d try to wrap the plywood before the laser cut.

The prior black ACM panel looked great.  But after ruining a $40 ACM panel on the CNC, I decided to not wait and buy another. The plywood + wrap can be cut with just a laser.

A low-mounted monitor under the table displays the Air Manager Manifold and Tach gauges. The monitor is secured with 3D-printed brackets, glued using construction adhesive. 

The model has an unused gauge cutout layer. I may build stepper motor versions for our oil, fuel, manifold and tach that match our real plane.

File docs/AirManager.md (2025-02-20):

# Air Manager

I purchased a copy of Air Manager two years ago for my first desktop sim and it’s the only component still used from that era, it's been reliable and a fun tool.  My current panel also has a knobster, unused now but available later.

## G5
The $25 Air Manager G5 was the best I found, more realistic than Asobo and without the pop-out hassles.  SIM Innovations makes Air Manager and has good instructions for using the RealSimGear bezel controls.  I also use the JPI EDM.

## Custom Instruments
I created my own instruments below.  I still use my Manifold and Tach gauges.  The 255 radio has been replaced with a much better hardware version and I'm not now using the others.  

### Garmin Radios
[Air Manager for Garmin](https://github.com/radiobillm/DakotaSim/archive/refs/tags/v1.0-airmanager-garmin.zip) zip file

#### GNC-255 Com-Nav Radio
GNC255
  
#### GTX-345 Transponder
GTX345

### Dakota Gauges and Lever
[Air Manager for Dakota](https://github.com/radiobillm/DakotaSim/releases/download/v1.0-airmanager-dakota/AirManager-Dakota.zip) zip file

#### Fuel Gauge
Air Manager Fuel Gauge

#### Oil Gauge
Air Manager Oil

#### Tach
Air Manager Tach

#### Manifold
Air Manager Mainford

#### Fuel Lever
Air Manager Fuel

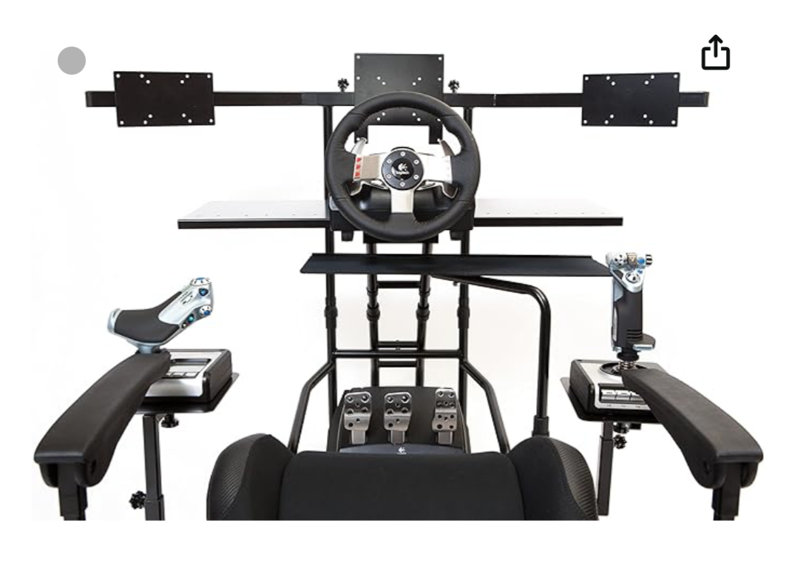
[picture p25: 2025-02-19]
docs/images/volair-chasis-front.jpeg

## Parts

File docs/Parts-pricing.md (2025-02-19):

## Parts and Prices

### Software

- $60 [Microsoft Flight Simulator 2020](https://www.xbox.com/en-US/games/microsoft-flight-simulator#purchaseoptions)
- $70 [TDS GTN](https://www.tdssim.com/tdsgtnxi)
- $25 [Air Manager G5](https://www.siminnovations.com/shop/garmin-g5/)
- $25 [SWS Vans RV-10](https://simworksstudios.com/rv10-msfs.html) (closest to PA28-235 with G3X)
- $47 [Just Flight PA-Arrow](https://www.justflight.com/product/pa-28r-arrow-iii-microsoft-flight-simulator)
- $0 [MSFS Popout Panel Manager](https://flightsim.to/file/35759/msfs-pop-out-panel-manager)
- $0 [MobiFlight](https://www.mobiflight.com/en/index.html)
- $0 [Little Navmap](https://albar965.github.io/littlenavmap.html)
- $50 [RealVNC](https://www.realvnc.com/en/)

### Computer

- $2800 [Windows i9/480 build](https://pcpartpicker.com/list/qsLdJy) in a mini ITX case

### Monitors and Sound

- $700 [Samsung Odyssey G9](https://www.amazon.com/gp/product/B0CP6HW894/) 49” Ultrawide monitor
- $250 Two [Samsung 27” T35F](https://www.amazon.com/gp/product/B08FF3JQ28/) side monitors
- $300 [Sonos Beam](https://www.sonos.com/en-us/shop/beam-b-stock-shadow), used Gen 1
- $85 [USB2GA Aviation Headset to USB Adapter](https://www.amazon.com/gp/product/B0CW3GLDM1/)

### Panel and Chassis

- $600 [Triple monitor stand from Simfab](https://simfab.com/product/triple-monitor-mount-stand/)
- $1000 [Volair chassis](https://volairsim.com/product/volair-sim-flight-racing-sim-cockpit/) with arm rests and keyboard mount
- $30 [Plywood, 5.2mm Sande](https://www.homedepot.com/pep/SANDEPLY-5-2mm-Sandeply-Plywood-1-4-in-Category-Common-1-4-in-x-4-ft-x-8-ft-Actual-0-205-in-x-48-in-x-96-in-479023/203414042)
- $20 [Auto Wrap](https://www.amazon.com/gp/product/B083KNZK5M/) for the panel surface
- $20 [Leather Repair Patch](https://www.amazon.com/gp/product/B0DRCFKVQK/) to cover the glare shield
- $20 [Neoprene Rubber](https://www.amazon.com/gp/product/B0B1M2LB9Z/) ¼” for the glare shield

### Instruments

- $1200 [G500](https://realsimgear.com/products/realsimgear-g500-avionics-panel)
- $550 [GTN650](https://realsimgear.com/products/realsimgear-gtn650-bezel-for-x-plane-p3d-and-fsx-steam)
- $350 [GFC500](https://realsimgear.com/products/realsimgear-gfc500-autopilot-for-x-plane-p3d-fsx)
- $350 [G5](https://realsimgear.com/products/realsimgear-g5-pfd-hsi-for-x-plane)
- $300 [GMA350](https://realsimgear.com/products/realsimgear-gma350-audio-panel-for-x-plane-p3d-fsx)
- $210 GNC255 Radio from Tigerfly Design

### Controls

- $920 [Flitesim CLS-60](https://flitesim.com/shop/p/cls-60) Yoke (including shipping)
- $600 [Thrustmaster TPR](https://www.amazon.com/dp/B07DQY8LVC) Pedals
- $130 [Throttle Cover](https://www.planeparts.com/cgi-bin/Web_store/web_store.cgi?product=Throttle28)
- $161 [Trim](https://www.desktopaviator.com/Products/Model_2700/index.htm) from Desktop Aviator (for parts)
- $80 [Flaps](https://www.desktopaviator.com/Products/Model_2530/index.htm) switch from Desktop Aviator (for parts)
- $50 [Ignition Key](https://www.ebay.com/itm/305096521217) from SimWales
- $60 [Parking brake](https://www.ebay.co.uk/itm/304357864568?itmmeta) from SimWales
- $90 [Compass](https://www.ebay.com/itm/304519129244) from SimWales

### Panel LCD Displays

- $70 [1920x1200](https://www.amazon.com/gp/product/B0DKFHZ8C8/) 14” left-side display for Air Manager compass, JPI engine, oil
- $70 [1024x600](https://www.amazon.com/gp/product/B07VNX4ZWY/?th=1) 7” right-side touch display for Air Manager radio and transponder
- $300 [1920x360](https://www.amazon.com/gp/product/B0CFY564ZQ) 24” low display for Air Manager fuel, manifold and tach

### Hubs, Power and Cables

- $180 for two [StarTech USB to 4x HDMI](https://www.amazon.com/gp/product/B09BJWGPXR/)
- $80 for two [Anker 10 Port 60W USB Hubs](https://www.amazon.com/gp/product/B00VDVCQ84/)
- $21 [USB A to TOSLINK](https://www.amazon.com/gp/product/B0B2DBGKL3/r) for Sonos Beam audio
- $20 [10A 12V Power supply](https://www.amazon.com/gp/product/B07MXXXBV8/) with custom hydra for RSG panel monitors
- $57 [8 Outlet Metal Power Strip](https://www.amazon.com/gp/product/B0CJ55M1TH/)
- $17 [LED Strip Lighting](https://www.amazon.com/gp/product/B0927CD434/r) 5mm for under glare shield
- $9 [LED dimmer](https://www.amazon.com/gp/product/B07WGT8K82/) dims the glare shield and compass LED
- $7 [Power Panel Mount](https://www.amazon.com/gp/product/B07CTCLKPP), 5.5mm 2 Pin
- $8 [12” USB-A Micro cable](https://www.amazon.com/gp/product/B095JZSHXQ/r)
- $8 [12” USB-A to C cables](https://www.amazon.com/gp/product/B0BDFHBXQC/r)
- $7 [18” HDMI cable](https://www.amazon.com/gp/product/B07ZC5Y3K2/r)
- $9 [12” HDMI cables](https://www.amazon.com/gp/product/B0B5KN6853/)
- $14 [6’ HDMI thin cables](https://www.amazon.com/gp/product/B00T58JLPI/r)
- $10 [Displayport to HDMI adapters](https://www.amazon.com/gp/product/B09MTKHFKR/)

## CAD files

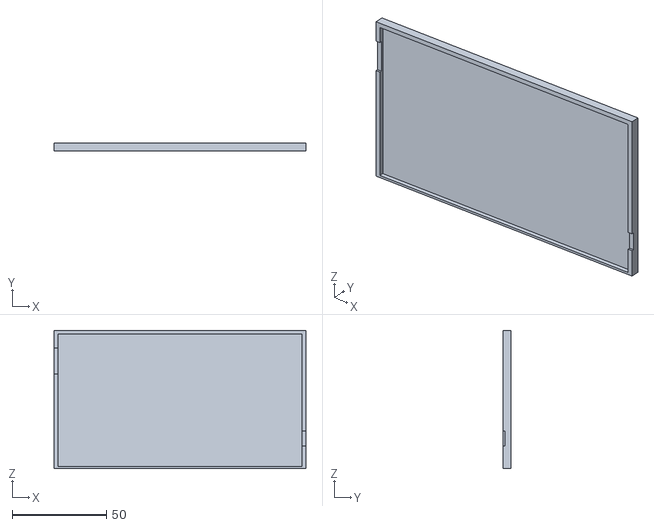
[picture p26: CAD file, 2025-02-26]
stl-dxf/lcd-box-top.stl
134.0 x 4.00 x 73.5

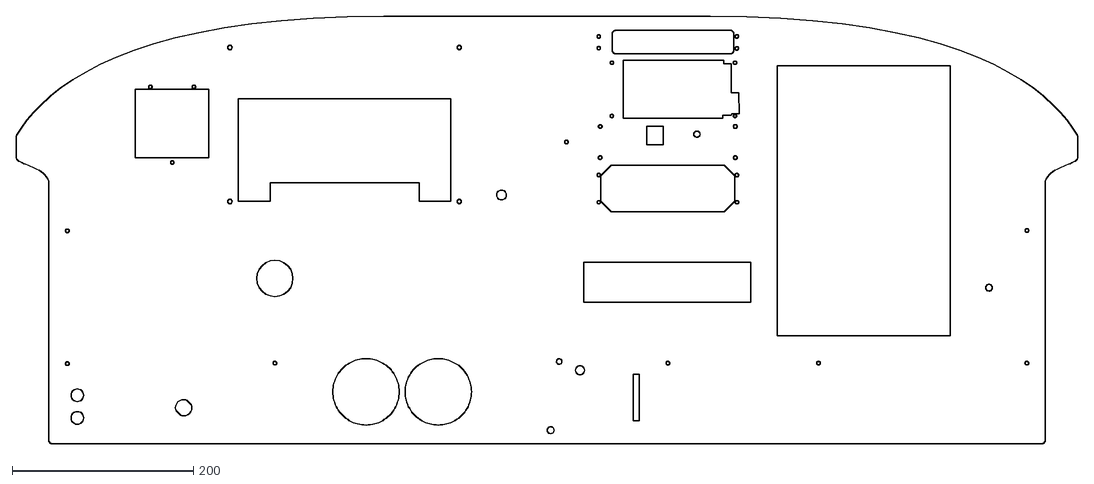
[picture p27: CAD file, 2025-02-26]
stl-dxf/panel-acm.dxf
1171.9 x 472.0

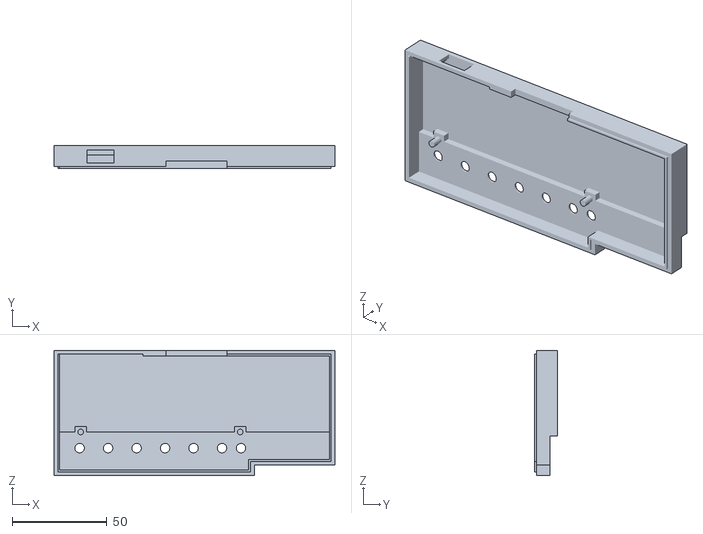
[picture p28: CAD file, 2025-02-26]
stl-dxf/tach-lcd-box-top.stl
148.0 x 12.0 x 66.0

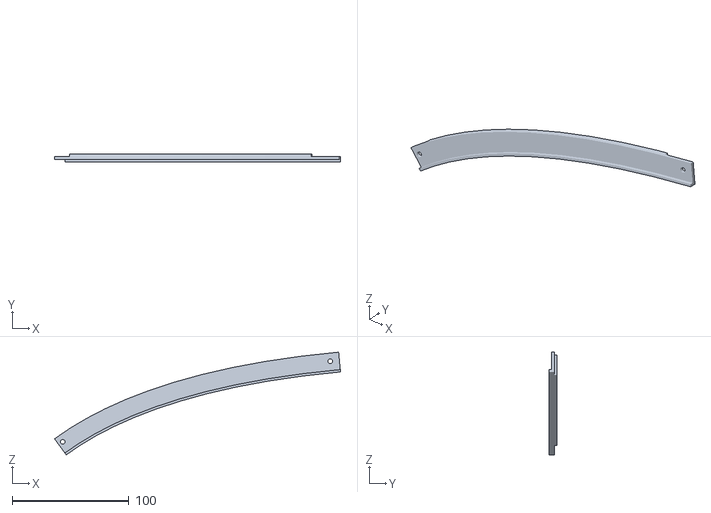
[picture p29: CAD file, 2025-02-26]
stl-dxf/cap-e.stl
244.8 x 7.06 x 87.9

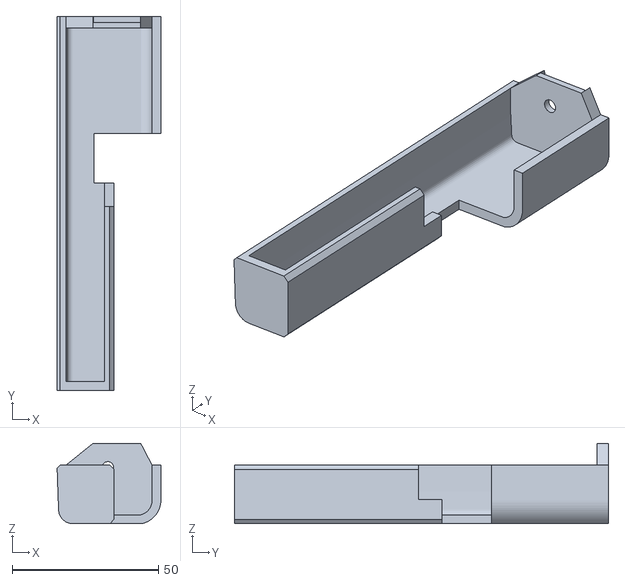
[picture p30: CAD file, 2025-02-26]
stl-dxf/cap-left.stl
35.5 x 128.0 x 27.5

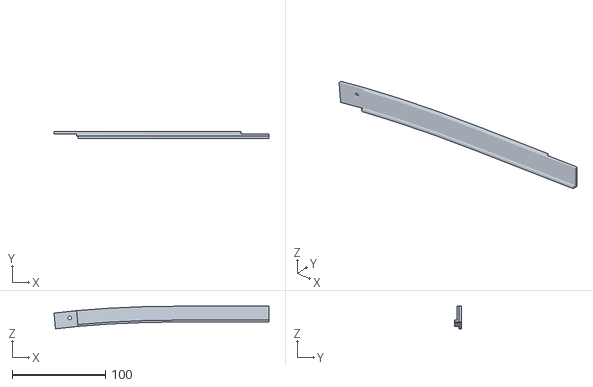
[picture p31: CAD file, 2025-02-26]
stl-dxf/cap-d.stl
230.8 x 7.08 x 24.4

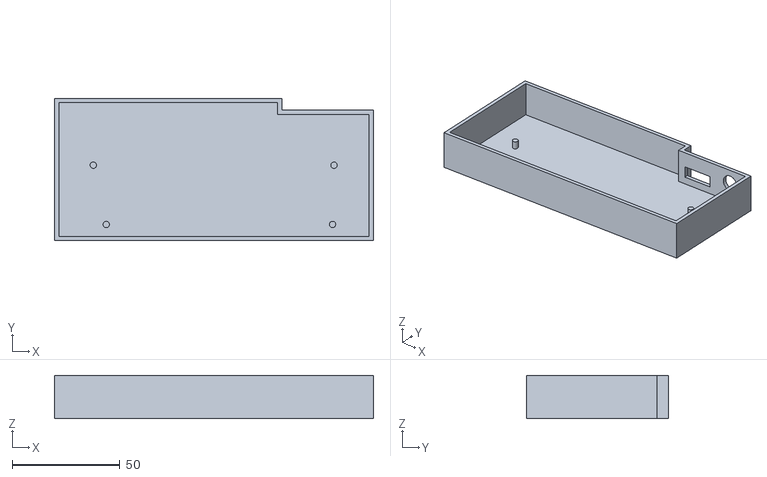
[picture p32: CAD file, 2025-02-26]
stl-dxf/tach-lcd-box-bottom.stl
148.0 x 66.0 x 20.0

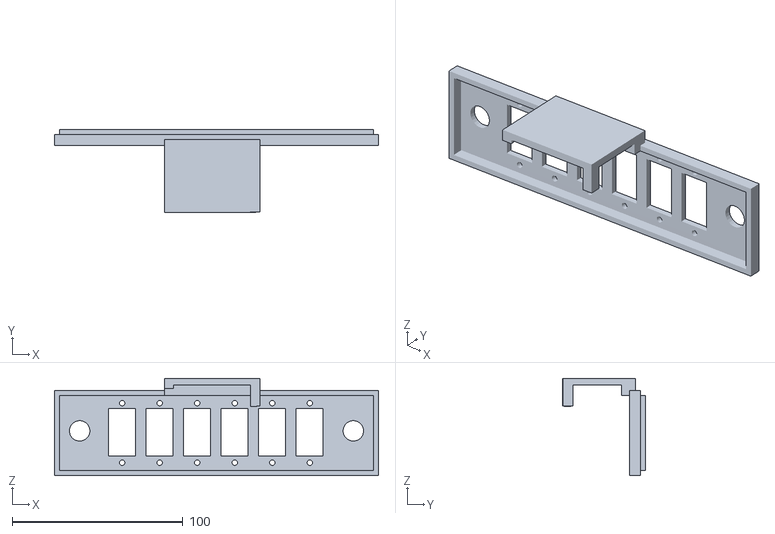
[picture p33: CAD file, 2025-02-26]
stl-dxf/switch.stl
190.0 x 48.4 x 57.0

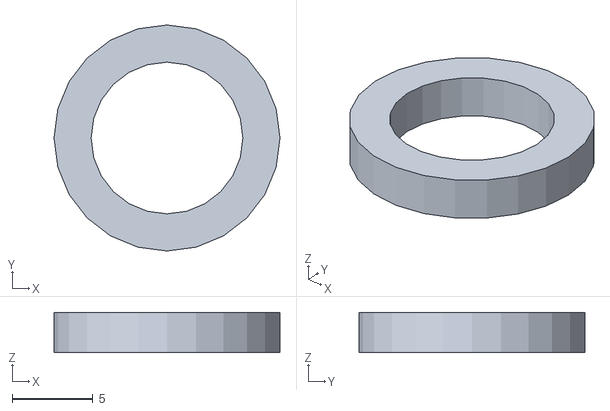
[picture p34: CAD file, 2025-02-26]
stl-dxf/headset-bushing.stl
14.0 x 14.0 x 2.50

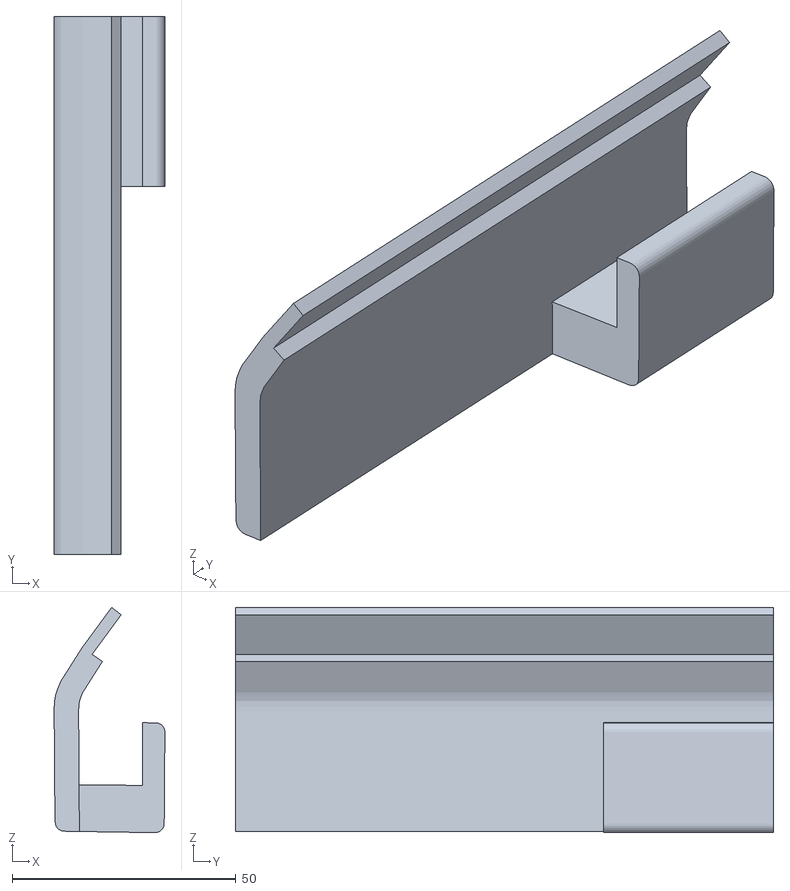
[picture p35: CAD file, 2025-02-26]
stl-dxf/end-left.stl
24.8 x 120.4 x 50.4

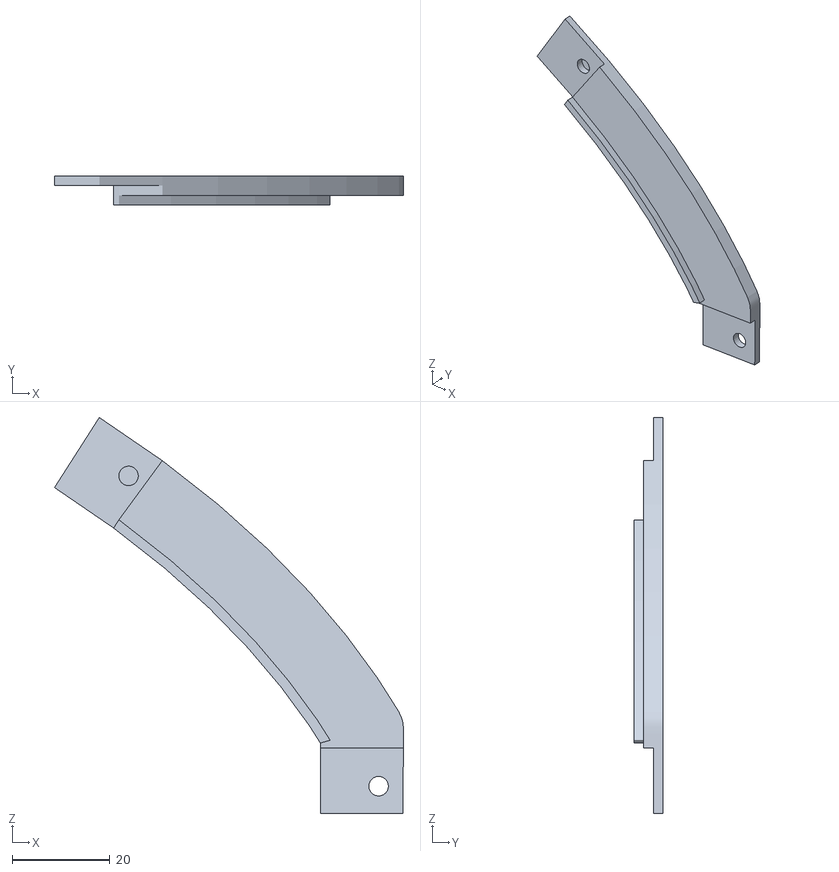
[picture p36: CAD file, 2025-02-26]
stl-dxf/cap-a.stl
71.4 x 6.00 x 81.0

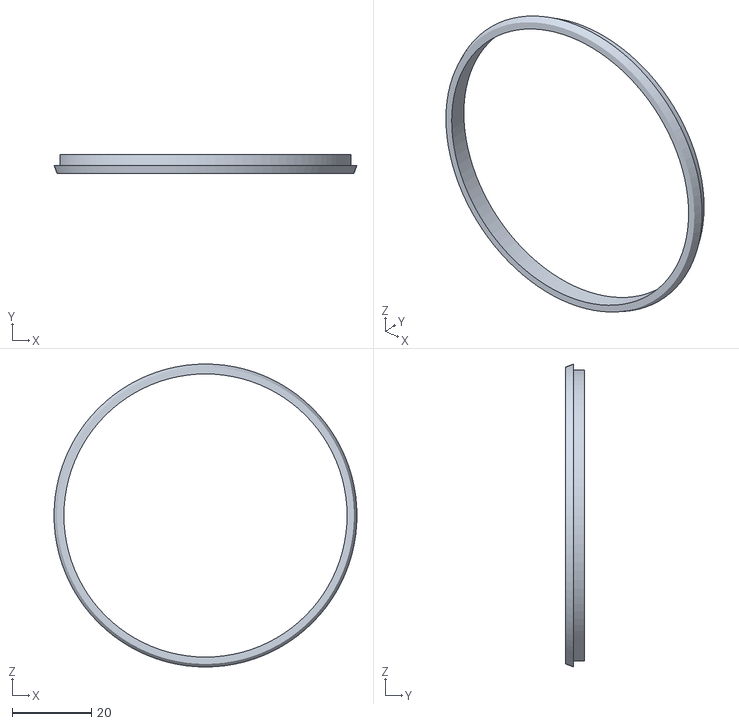
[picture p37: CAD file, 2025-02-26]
stl-dxf/tach-bezel.stl
76.4 x 4.70 x 76.4

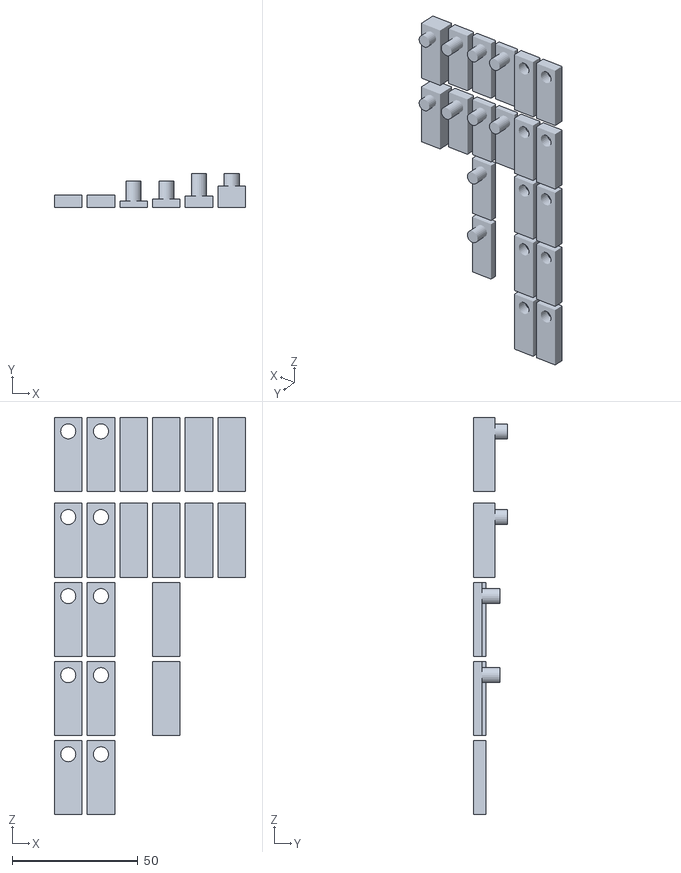
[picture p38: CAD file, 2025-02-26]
stl-dxf/clip.stl
76.0 x 13.6 x 157.8

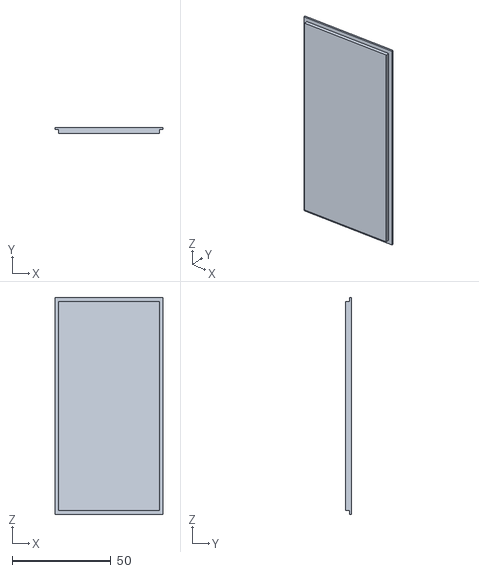
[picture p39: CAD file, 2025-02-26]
stl-dxf/dimmer-housing-lid.stl
55.0 x 3.00 x 110.0

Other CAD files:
stl-dxf/cap-c.stl
stl-dxf/switch-mount.stl
stl-dxf/cap-b.stl
stl-dxf/sim.dxf
sketchup/dakota-honeycomb.skp
stl-dxf/cap-f.stl
stl-dxf/cap-right.stl
stl-dxf/dakota-sim-panel-laser.dxf
stl-dxf/dimmer-housing.stl
stl-dxf/lcd-box-bottom.stl
stl-dxf/lcd-clip.stl
stl-dxf/panel-ply.dxf
stl-dxf/tach-lcd-box.stl

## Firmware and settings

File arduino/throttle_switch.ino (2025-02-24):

#include <Joystick.h>

// Create the Joystick object
Joystick_ Joystick(JOYSTICK_DEFAULT_REPORT_ID, JOYSTICK_TYPE_GAMEPAD, 19, 0, true, true, true);

// Analog input pins for axes
const int axisPins[] = {A0, A1, A2}; // Throttle, Mixture, Prop

// Digital input pins for switches
const int buttonPins[] = {
    12, // Avionics On
    11, // Avionics Off
    10, // Master On
    9,  // Master Off
    8,  // Fuel On
    7,  // Fuel Off
    6,  // Landing On
    2,  // Landing Off
    5,  // Beacon On
    4,  // Beacon Off
    3,  // Collision On
    0,  // Collision Off
    1,  // Pitot On
    13, // Pitot Off
    16, // Nav On
    15, // Nav Off
    A3, // Carb Heat On
    A4, // Carb Heat Off
    14  // GA
};

// Number of axes and buttons
const int axisCount = sizeof(axisPins) / sizeof(axisPins[0]);
const int buttonCount = sizeof(buttonPins) / sizeof(buttonPins[0]);

// State tracking for switches and axes
bool lastState[buttonCount] = {false};
int lastAxisValue[axisCount] = {0};

// Predefined min and max values for each axis
const int axisMin[axisCount] = {425, 430, 470}; // Throttle, Mixture, Prop
const int axisMax[axisCount] = {825, 850, 866};

// Define the size of the moving average buffer
const int bufferSize = 5;
int axisBuffers[axisCount][bufferSize] = {0};
int bufferIndex[axisCount] = {0};

// Dead zone threshold to ignore minor fluctuations
const int deadZone = 5; // Adjust this value based on your needs

int calculateAverage(int axisIndex) {
    int sum = 0;
    for (int j = 0; j < bufferSize; j++) {
        sum += axisBuffers[axisIndex][j];
    }
    return sum / bufferSize;
}

void setup() {
    // Initialize the Serial Monitor
    Serial.begin(9600);

    // Initialize the Joystick library
    Joystick.setXAxisRange(0, 1023);
    Joystick.setYAxisRange(0, 1023);
    Joystick.setZAxisRange(0, 1023);
    Joystick.begin();

    // Configure axis pins as input
    for (int i = 0; i < axisCount; i++) {
        pinMode(axisPins[i], INPUT);
    }

    // Configure button pins as input with pull-up
    for (int i = 0; i < buttonCount; i++) {
        pinMode(buttonPins[i], INPUT_PULLUP);
    }
}

void loop() {
    int normalizedValues[axisCount];

    // Read and update axes
    for (int i = 0; i < axisCount; i++) {
        int axisValue = analogRead(axisPins[i]);

        // Add the raw value to the buffer for smoothing
        axisBuffers[i][bufferIndex[i]] = axisValue;
        bufferIndex[i] = (bufferIndex[i] + 1) % bufferSize; // Circular buffer

        // Calculate the smoothed value
        int smoothedValue = calculateAverage(i);

        // Map the smoothed values to the full range (0–1023)
        int normalizedValue = map(smoothedValue, axisMin[i], axisMax[i], 0, 1023);

        // Ensure the value stays within bounds
        normalizedValue = constrain(normalizedValue, 0, 1023);

        // Apply dead zone: only update if the change is greater than the threshold
        if (abs(normalizedValue - lastAxisValue[i]) > deadZone) {
            lastAxisValue[i] = normalizedValue;

            // Send the value to the joystick and log it
            switch (i) {
                case 0:
                    Joystick.setXAxis(normalizedValue);
                    Serial.print("USB X sent: ");
                    break;
                case 1:
                    Joystick.setYAxis(normalizedValue);
                    Serial.print("USB Y sent: ");
                    break;
                case 2:
                    Joystick.setZAxis(normalizedValue);
                    Serial.print("USB Z sent: ");
                    break;
            }
            Serial.println(normalizedValue); // Print the value sent
        }
        normalizedValues[i] = normalizedValue;
    }

    // Read and update button states
    for (int i = 0; i < buttonCount; i++) {
        bool currentState = digitalRead(buttonPins[i]) == LOW; // Active LOW
        if (currentState != lastState[i]) {
            lastState[i] = currentState;
            Joystick.setButton(i, currentState);
       }
    }

    // Small delay for stability
    delay(100);
}

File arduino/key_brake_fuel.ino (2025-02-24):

#include <Joystick.h>

// Create the Joystick object
Joystick_ Joystick(JOYSTICK_DEFAULT_REPORT_ID, JOYSTICK_TYPE_GAMEPAD, 12, 0, false, false, true); // 12 buttons, Z-axis only

// Pin assignments for HID buttons
const int buttonPins[] = {
    2, 3, 4, 5, 6, 14, 16, 21, 20, 19, 18, 15
};

// Names for debugging
const char* buttonNames[] = {
    "Key Off", "Key A", "Key B", "Key Run", "Key Start",
    "Park Off", "Park On", "Fuel Off",
    "Left Tip", "Left Main", "Right Main", "Right Tip"
};

// Number of buttons
const int buttonCount = sizeof(buttonPins) / sizeof(buttonPins[0]);

// Pin for rudder trim potentiometer
const int rudderTrimPin = A8;

// State tracking for switches
bool lastState[buttonCount] = {false};

void setup() {
    // Initialize the Joystick library
    Joystick.setZAxisRange(-32767, 32767);
    Joystick.begin();

    // Configure button pins as input with pull-up
    for (int i = 0; i < buttonCount; i++) {
        pinMode(buttonPins[i], INPUT_PULLUP);
    }

    // Configure the rudder trim potentiometer pin
    pinMode(rudderTrimPin, INPUT);
}

void loop() {
    // Read and update button states
    for (int i = 0; i < buttonCount; i++) {
        bool currentState = digitalRead(buttonPins[i]) == LOW; // Active LOW
        if (currentState != lastState[i]) {
            lastState[i] = currentState;
            Joystick.setButton(i, currentState);
        }
    }

    // Read and map the rudder trim potentiometer value
    int rudderTrimValue = analogRead(rudderTrimPin);
    int mappedValue = map(rudderTrimValue, 0, 1023, -32767, 32767);
    Joystick.setZAxis(mappedValue);

    // Small delay for stability
    delay(50);
}
